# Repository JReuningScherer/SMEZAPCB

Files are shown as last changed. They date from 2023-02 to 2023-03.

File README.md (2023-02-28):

# Team Solar - SMEZA PCB Repository

This is the repository for the PCB for the SMEZA. 

Code for the SMEZA should not be stored here - put those files in the [Team-Solar](https://github.com/kyperrone/Team-Solar) repo. 

We are using KiCad 7 for this project, as well as the following extensions:
- Freerouting extension, provided by the Official KiCad Repository. 
- Bounti's JLCPCB extension. This is in a [separate repository](https://github.com/Bouni/kicad-jlcpcb-tools) that must be added. 

# Explaination of Contents 
`smeza_pcb` - This folder contains the KiCad project files for the SMEZA PCB. 

`footprints` - This folder contains all of the project specific footprints in a convenient location. The footprint names in this folder are less than useful, so there is a README file that indicates which file is for which component. 

`symbols` - This folder contains all of the project specific symbols and footprints. Each component has its own folder. 

# Getting Started with using this repo 
I don't know how familiar everyone is with Git so I'm going to say a few things that are probably obvious to more experienced users. 

The primary branch for this repo is `main`. 

Please don't commit directly to main; make a branch for your changes and then when you are done make a pull-request. 

When possible, it is preferred that you obtain this repo by cloning it. However, since most Valpo machines do not have git it may be necessary to download the files and then try to merge after the fact. This is another good time to use a branch incase things get messed up. It should be noted that the 4-machines in the team solar senior design space have git installed - just make sure to use the git-bash terminal. 

While the KiCad files are technically text files, because of the large scale of changes made by even small changes, best practice is probably to clobber everything in `main` with the contents of the newer branch. 

If you have questions about using git, talk to Joel.

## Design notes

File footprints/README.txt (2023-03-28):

Tranceiver: ADM4852ARZ.kicad_mod

H-Bridge: SOIC100P600X175-10N.kicad_mod
H-Bridge Alternate: A3909GLYTR-T.kicad_mod

Buck Converter (MP4541): SOIC127P600X170-9N.kicad_mod

RJ-45: SS90000002.kicad_mod

Oscillator: OSC_CSTNE16M0V530000R0.kicad_mod

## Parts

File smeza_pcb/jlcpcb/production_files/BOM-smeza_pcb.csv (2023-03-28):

Comment | Designator | Footprint | LCSC
10uF | C2A1,C2B1,C8 | C_1206_3216Metric | C13585
ATmega328P-A | U2 | TQFP-32_7x7mm_P0.8mm | C14877
100k | R8 | R_0805_2012Metric | C149504
680pF | C1 | C_0603_1608Metric | C1630
1.2k | R1 | R_0805_2012Metric | C17379
1.8k | R6 | R_0805_2012Metric | C17398
10k | R14,R15,R2 | R_0805_2012Metric | C17414
120 | R22,R4 | R_0805_2012Metric | C17437
2.2k | R16,R17 | R_0805_2012Metric | C17520
27k | R12,R13 | R_0805_2012Metric | C17593
4.7k | R19,R20,R21 | R_0805_2012Metric | C17673
82k | R10,R11,R7 | R_0805_2012Metric | C17840
1uF | C5,C6 | C_1206_3216Metric | C1848
33uH | L1 | L_Taiyo-Yuden_NR-60xx_HandSoldering | C2049900
LED | D1 | LED_0603_1608Metric | C2286
0.1uF | C3,C4,C7 | C_1206_3216Metric | C24497
39k | R18 | R_0805_2012Metric | C25826
H_Bridge | H1 | SOIC100P600X175-10N | C2653462
CSTNE16M0V530000R0 | Y1 | OSC_CSTNE16M0V530000R0 | C341521
5.6k | R5,R9 | R_0805_2012Metric | C4382
1k | R3 | R_1206_3216Metric | C4410
2.2uF | C2 | C_1206_3216Metric | C50254
1nF | C10,C11,C9 | C_1206_3216Metric | C9196
MP4541GN-Z | B1 | SOIC127P600X170-9N
LM317_TO-220 | U1 | TO-220-3_Vertical

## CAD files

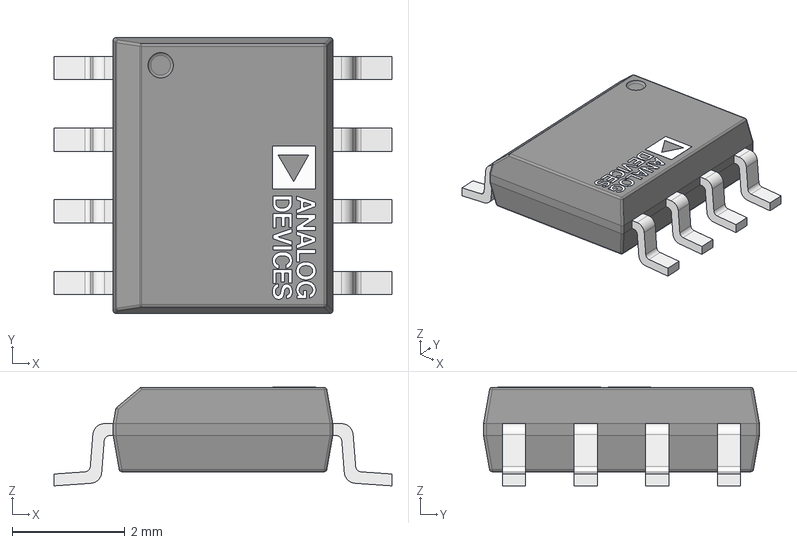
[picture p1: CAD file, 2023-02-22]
symbols/ADM4852ARZ/eec.models/Analog_Devices_-_ADM4852ARZ.step
6.00 x 4.90 x 1.75 mm
pins
part number

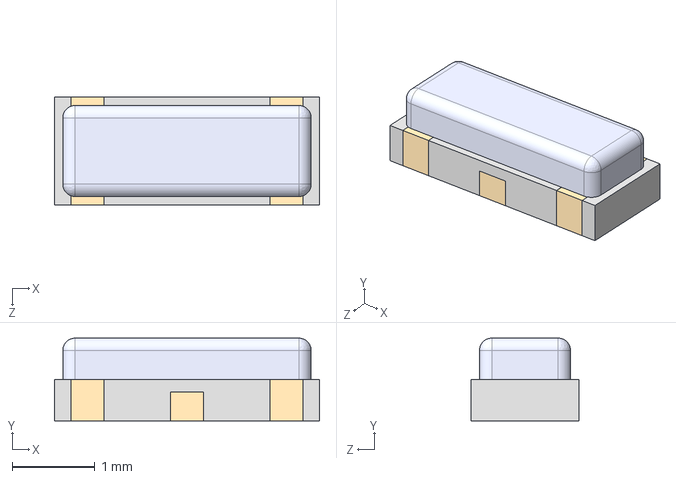
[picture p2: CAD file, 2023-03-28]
symbols/CSTNE16M0V530000R0/CSTNE16M0V530000R0.step
3.20 x 1.00 x 1.30 mm

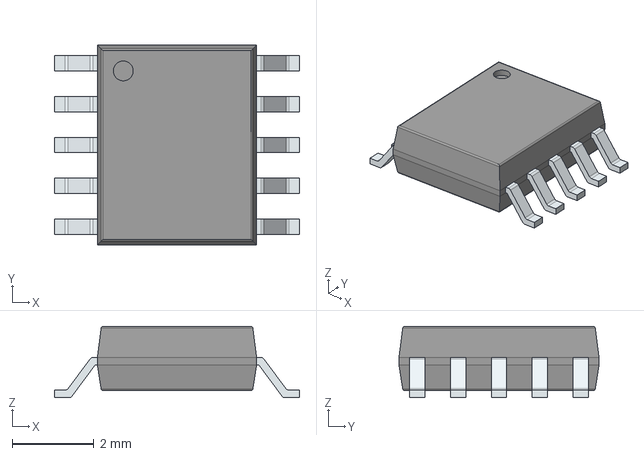
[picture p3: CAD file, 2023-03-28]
symbols/LIB_A3909GLNTR-T/A3909GLNTR-T/3D/A3909GLNTR-T.stp
6.00 x 4.90 x 1.75 mm
PinsArrayLR

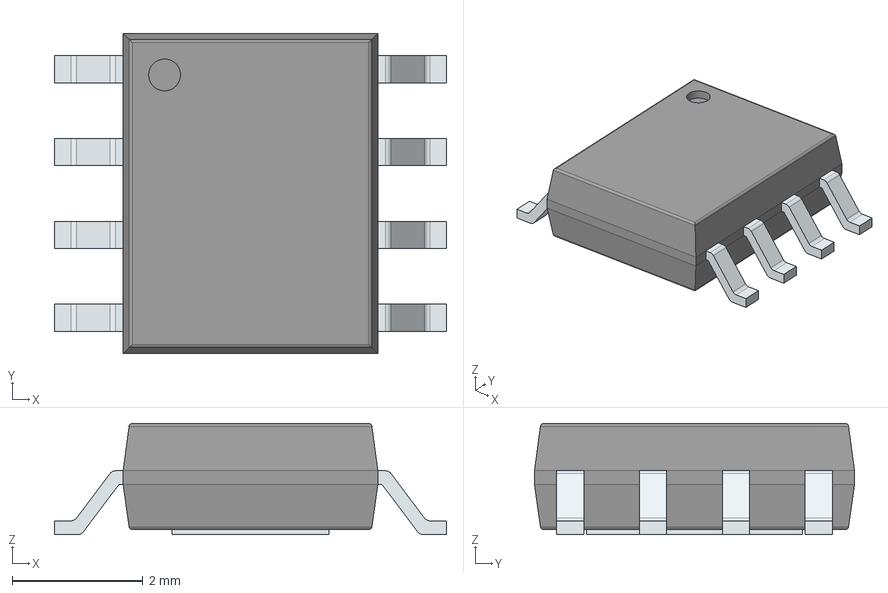
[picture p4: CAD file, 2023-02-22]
symbols/LIB_MP4541GN-Z/MP4541GN-Z/3D/MP4541GN-Z.stp
6.00 x 4.90 x 1.70 mm
PinsArrayLR
ThermalPad

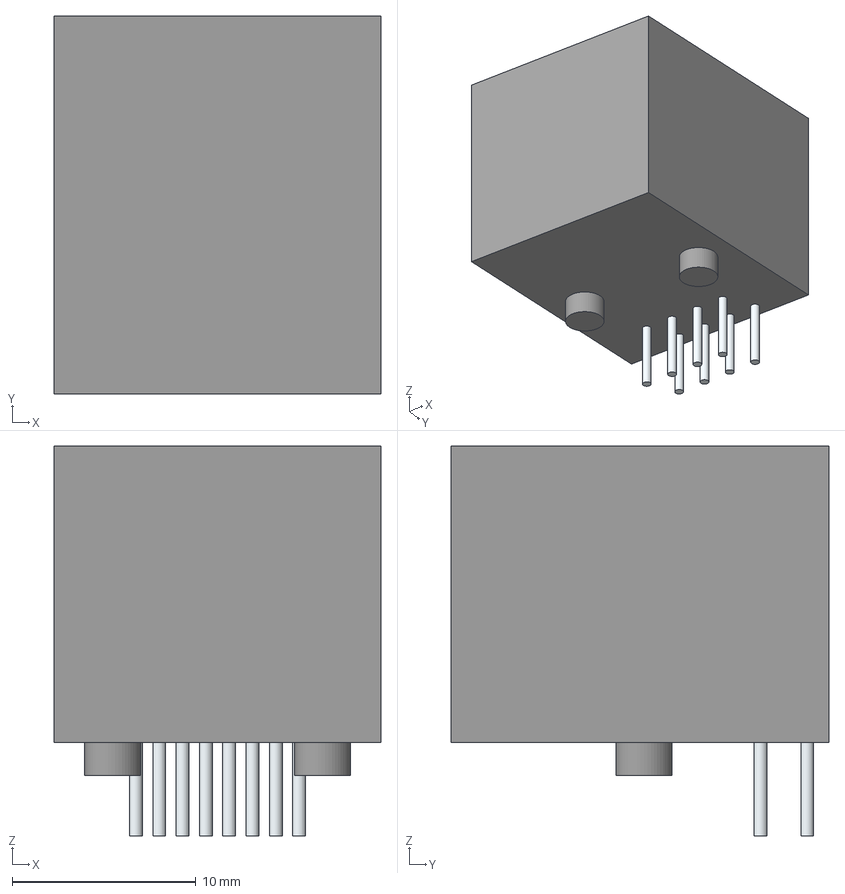
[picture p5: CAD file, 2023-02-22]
symbols/LIB_SS-90000-002/SS-90000-002/3D/SS-90000-002.stp
17.8 x 20.6 x 21.2 mm
Lugs
Leads

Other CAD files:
symbols/LIB_A3909GLNTR-T/A3909GLNTR-T/Allegro/sop100p600x175-10n.psm
symbols/LIB_A3909GLNTR-T/A3909GLNTR-T/DEHDL/a3909glntr_t/chips/chips.prt
symbols/LIB_MP4541GN-Z/MP4541GN-Z/Allegro/soic127p600x170-9n.psm
symbols/LIB_MP4541GN-Z/MP4541GN-Z/DEHDL/mp4541gn_z/chips/chips.prt
symbols/LIB_SS-90000-002/SS-90000-002/Allegro/ss90000002.psm
symbols/LIB_SS-90000-002/SS-90000-002/DEHDL/ss_90000_002/chips/chips.prt

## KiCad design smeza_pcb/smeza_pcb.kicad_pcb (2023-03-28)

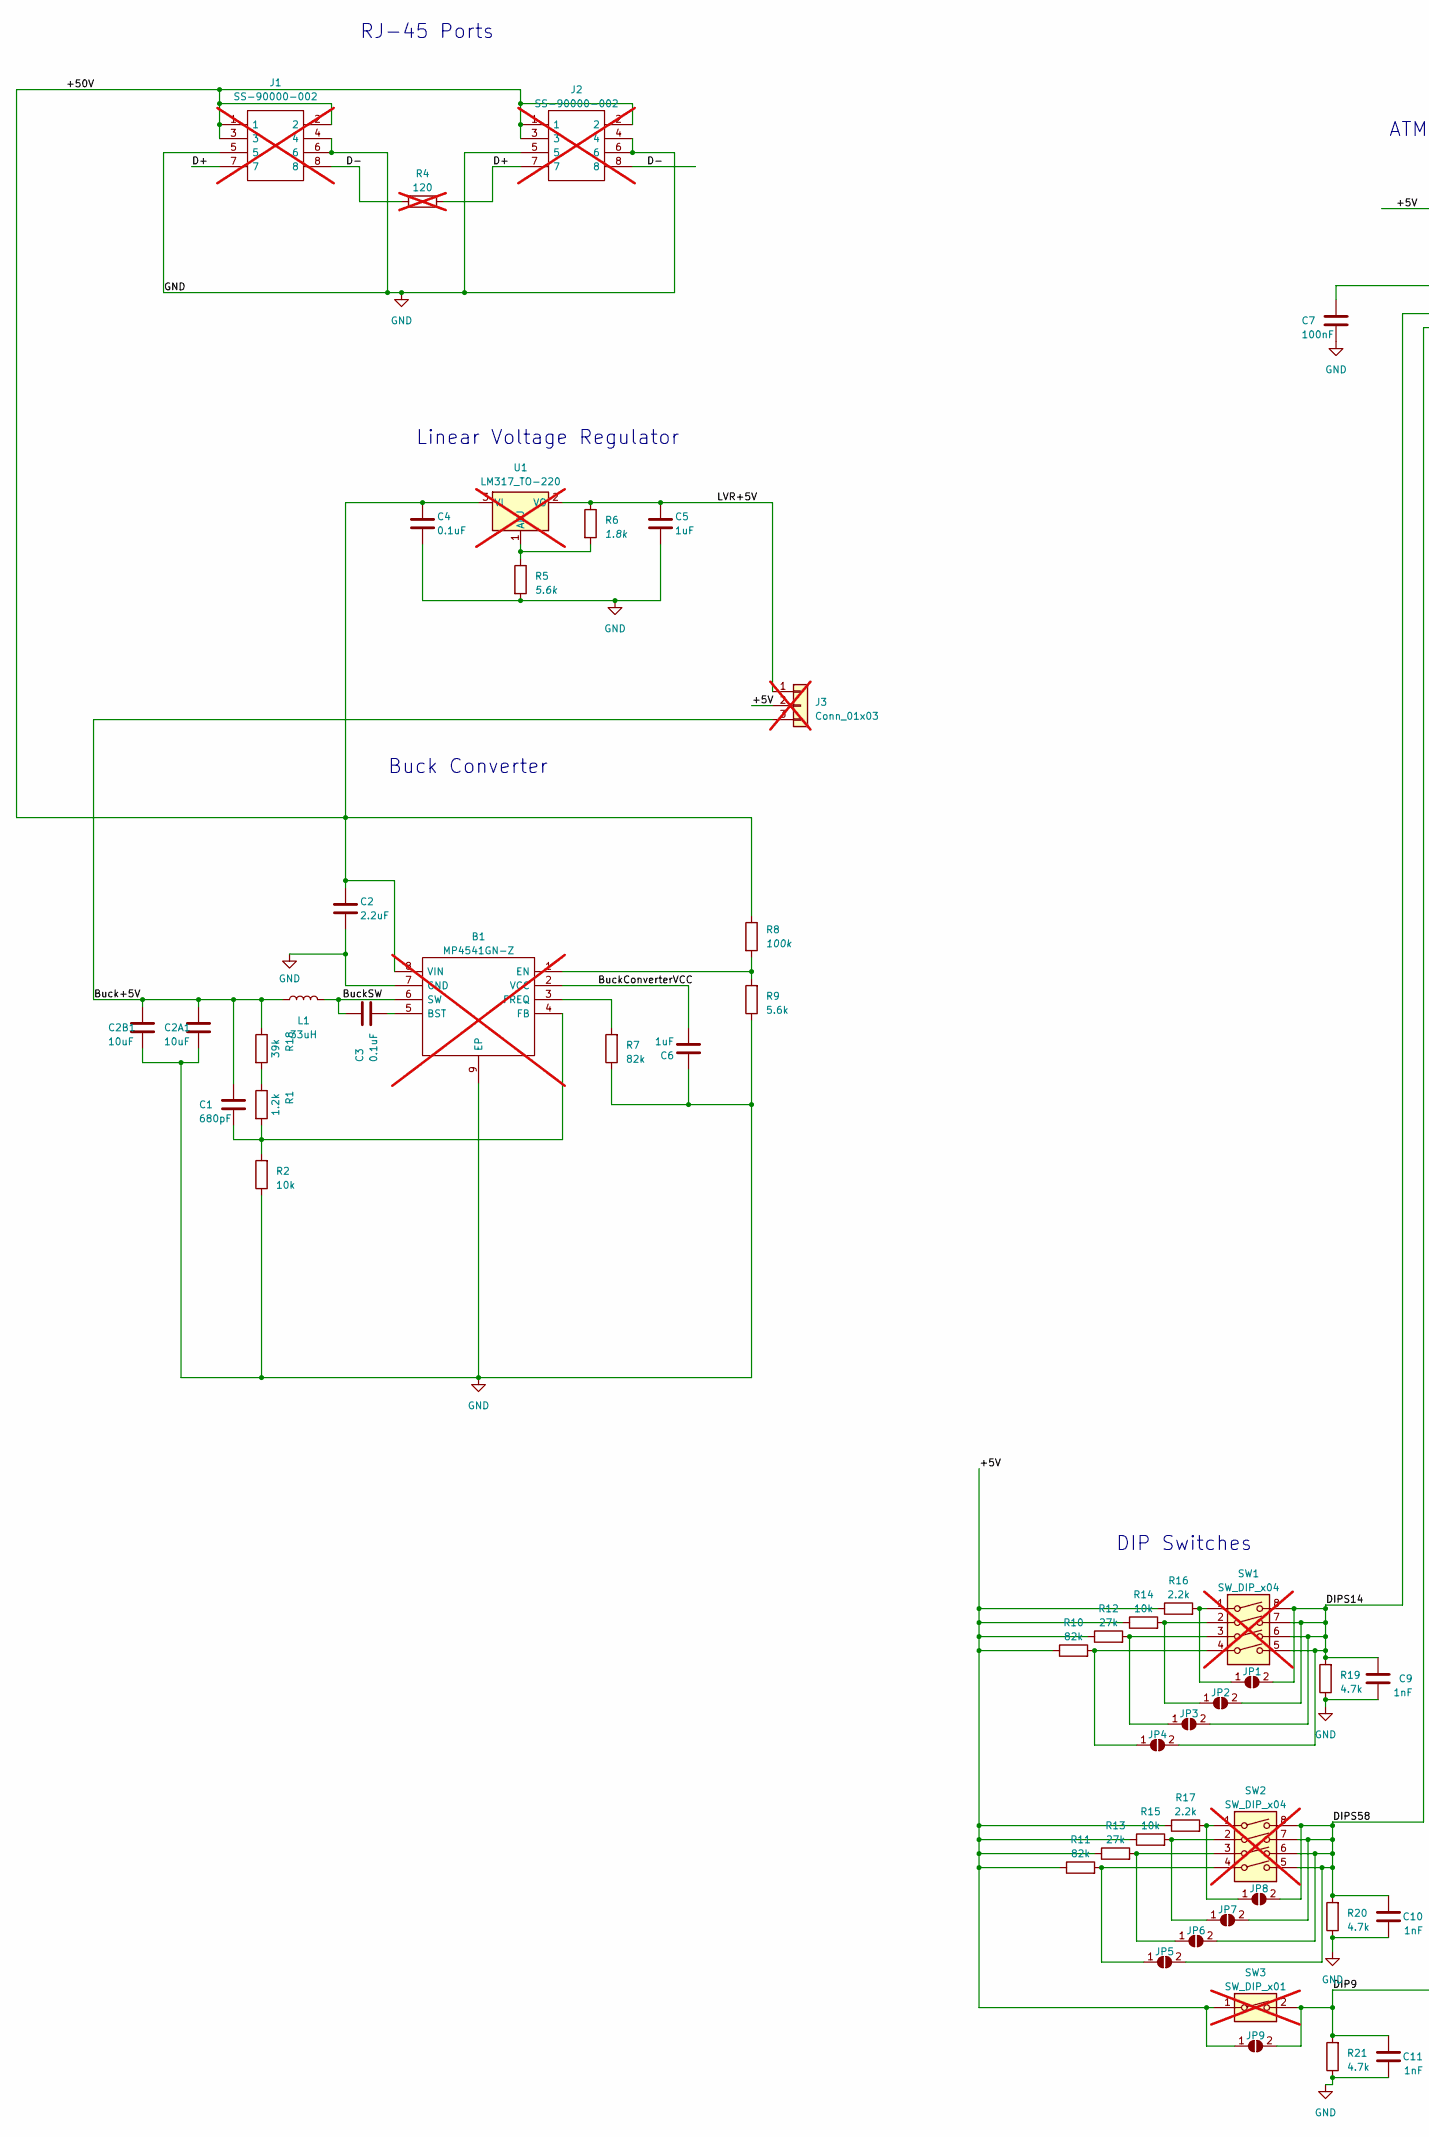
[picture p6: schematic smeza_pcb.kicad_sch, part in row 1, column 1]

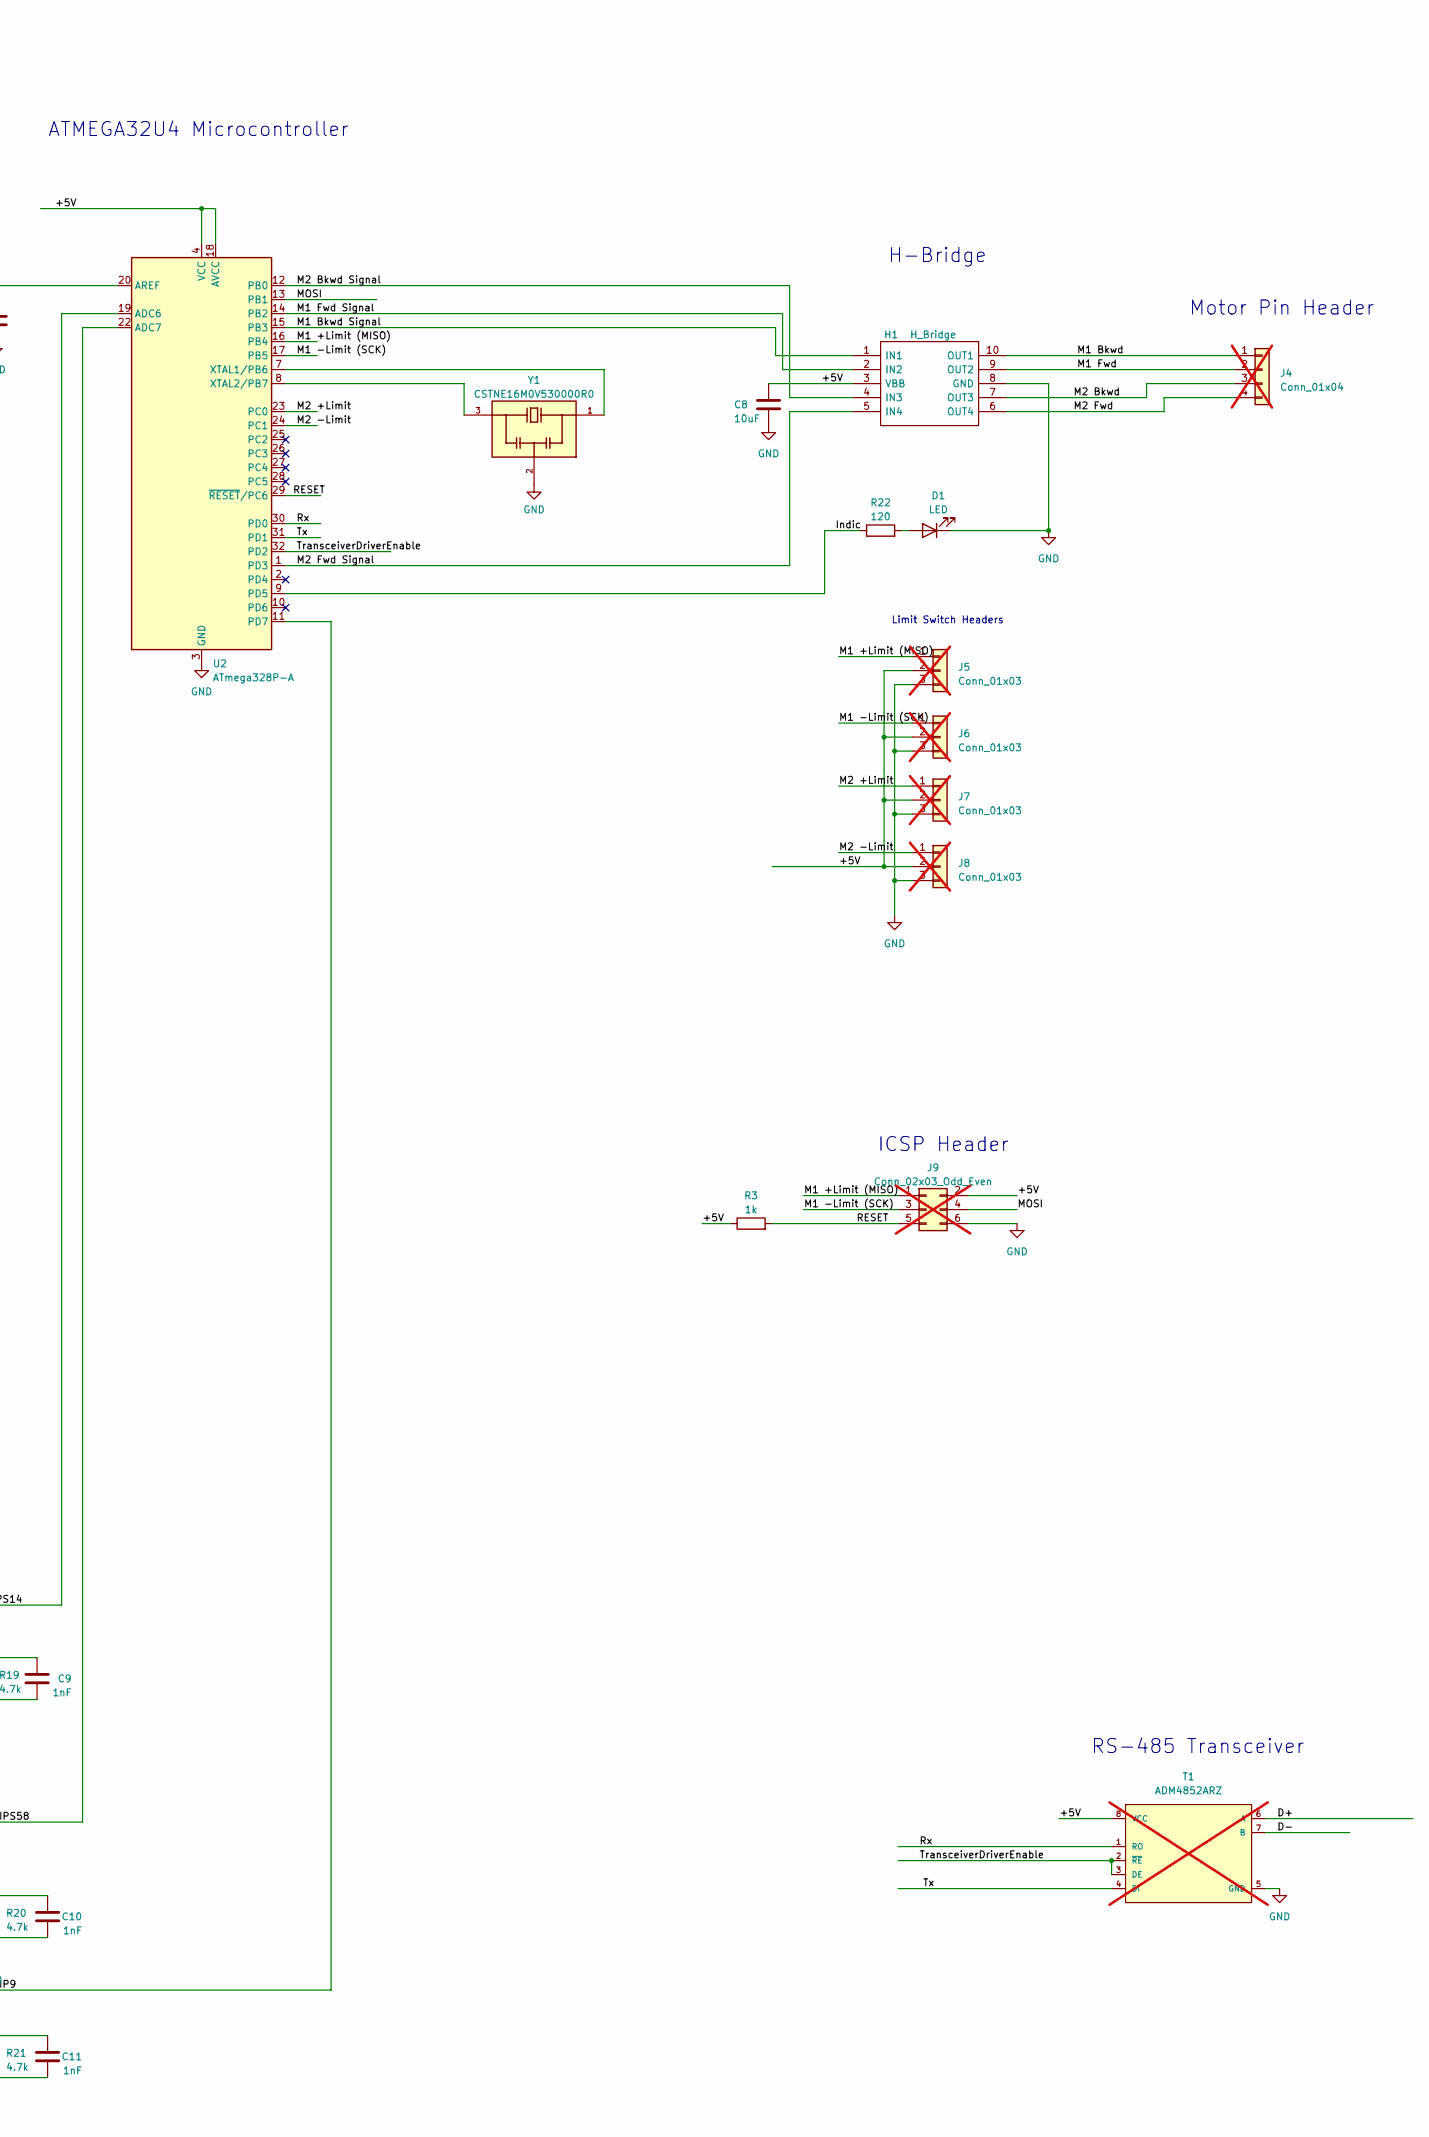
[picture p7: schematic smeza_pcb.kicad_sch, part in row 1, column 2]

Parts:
B1: MP4541GN-Z; SOIC127P600X170-9N; Mouser Part Number 946-MP4541GN-Z; not fitted
C1: 680pF; C_0603_1608Metric
C2: 2.2uF; C_1206_3216Metric
C2A1, C2B1, C8: 10uF; C_1206_3216Metric
C3, C4: 0.1uF; C_1206_3216Metric
C5, C6: 1uF; C_1206_3216Metric
C7: 100nF; C_1206_3216Metric
C9, C10, C11: 1nF; C_1206_3216Metric
D1: LED; LED_0603_1608Metric
H1: H_Bridge; SOIC100P600X175-10N; Manufacturer_Part_Number A3909GLNTR-T; Mouser Part Number 250-A3909GLNTR-T
J1, J2: SS-90000-002; SS90000002; Mouser Part Number 530-SS-90000-002; not fitted
J3: Conn_01x03; PinHeader_1x03_P2.54mm_Vertical; not fitted
J4: Conn_01x04; Molex_KK-254_AE-6410-04A_1x04_P2.54mm_Vertical; not fitted
J5, J6, J7, J8: Conn_01x03; Molex_KK-254_AE-6410-03A_1x03_P2.54mm_Vertical; not fitted
J9: Conn_02x03_Odd_Even; PinHeader_2x03_P2.54mm_Vertical; not fitted
JP1, JP2, JP3, JP4, JP5, JP6, JP7, JP8, JP9: SolderJumper_2_Open; SolderJumper-2_P1.3mm_Open_TrianglePad1.0x1.5mm
L1: 33uH; L_Taiyo-Yuden_NR-60xx_HandSoldering
R1: 1.2k; R_0805_2012Metric
R2, R14, R15: 10k; R_0805_2012Metric
R3: 1k; R_1206_3216Metric
R4: 120; R_0805_2012Metric; not fitted
R5, R9: 5.6k; R_0805_2012Metric
R6: 1.8k; R_0805_2012Metric
R7, R10, R11: 82k; R_0805_2012Metric
R8: 100k; R_0805_2012Metric
R12, R13: 27k; R_0805_2012Metric
R16, R17: 2.2k; R_0805_2012Metric
R18: 39k; R_0805_2012Metric
R19, R20, R21: 4.7k; R_0805_2012Metric
R22: 120; R_0805_2012Metric
SW1, SW2: SW_DIP_x04; SW_DIP_SPSTx04_Slide_9.78x12.34mm_W7.62mm_P2.54mm; not fitted
SW3: SW_DIP_x01; SW_DIP_SPSTx01_Slide_9.78x4.72mm_W7.62mm_P2.54mm; not fitted
T1: ADM4852ARZ; mouser part number 584-ADM4852ARZ; digikey description IC TRANSCEIVER HALF 1/1 8SOIC; not fitted
U1: LM317_TO-220; TO-220-3_Vertical; not fitted
U2: ATmega328P-A; TQFP-32_7x7mm_P0.8mm
Y1: CSTNE16M0V530000R0; OSC_CSTNE16M0V530000R0; PARTREV JGC42-8853B

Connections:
/+5V: C8.1, H1.3 (VBB), J3.2, J5.2, J6.2, J7.2, J8.2, J9.2, JP9.1 (A), R3.1, R10.1, R11.1, R12.1, R13.1, R14.1, R15.1, R16.1, R17.1, SW3.1, T1.8 (VCC), U2.4 (VCC), U2.6 (VCC), U2.18 (AVCC)
/+50V: B1.8 (VIN), C2.1, C4.1, J1.1, J1.2, J1.3, J2.1, J2.2, J2.3, R8.1, U1.3 (VI)
/Buck+5V: C1.1, C2A1.1, C2B1.1, J3.3, L1.1, R18.1
/BuckConverterVCC: B1.2 (VCC), C6.2
/BuckSW: B1.6 (SW), C3.1, L1.2
/D+: J1.7, J2.7, R4.1, T1.6 (A)
/D-: J1.8, J2.8, R4.2, T1.7 (B)
/DIP9: C11.1, JP9.2 (B), R21.2, SW3.2, U2.11 (PD7)
/DIPS14: C9.1, JP1.2 (B), JP2.2 (B), JP3.2 (B), JP4.2 (B), R19.2, SW1.5, SW1.6, SW1.7, SW1.8, U2.19 (ADC6)
/DIPS58: C10.1, JP5.2 (B), JP6.2 (B), JP7.2 (B), JP8.2 (B), R20.2, SW2.5, SW2.6, SW2.7, SW2.8, U2.22 (ADC7)
/Indic: R22.1, U2.9 (PD5)
/LVR+5V: C5.1, J3.1, R6.1, U1.2 (VO)
/M1 +Limit (MISO): J5.1, J9.1, U2.16 (PB4)
/M1 -Limit (SCK): J6.1, J9.3, U2.17 (PB5)
/M1 Bkwd: H1.10 (OUT1), J4.1
/M1 Bkwd Signal: H1.1 (IN1), U2.15 (PB3)
/M1 Fwd: H1.9 (OUT2), J4.2
/M1 Fwd Signal: H1.2 (IN2), U2.14 (PB2)
/M2 +Limit: J7.1, U2.23 (PC0)
/M2 -Limit: J8.1, U2.24 (PC1)
/M2 Bkwd: H1.7 (OUT3), J4.3
/M2 Bkwd Signal: H1.4 (IN3), U2.12 (PB0)
/M2 Fwd: H1.6 (OUT4), J4.4
/M2 Fwd Signal: H1.5 (IN4), U2.1 (PD3)
/MOSI: J9.4, U2.13 (PB1)
/RESET: J9.5, R3.2, U2.29 (~RESET/PC6)
/Rx: T1.1 (RO), U2.30 (PD0)
/TransceiverDriverEnable: T1.2 (~RE), T1.3 (DE), U2.32 (PD2)
/Tx: T1.4 (DI), U2.31 (PD1)
GND: B1.7 (GND), B1.9 (EP), C2.2, C2A1.2, C2B1.2, C4.2, C5.2, C6.1, C7.2, C8.2, C9.2, C10.2, C11.2, D1.1 (K), H1.8 (GND), J1.4, J1.5, J1.6, J2.4, J2.5, J2.6, J5.3, J6.3, J7.3, J8.3, J9.6, R2.1, R5.2, R7.1, R9.1, R19.1, R20.1, R21.1, T1.5 (GND), U2.3 (GND), U2.5 (GND), U2.21 (GND), Y1.2
unnamed: B1.5 (BST), C3.2
unnamed: B1.1 (EN), R8.2, R9.2
unnamed: B1.4 (FB), C1.2, R1.2, R2.2
unnamed: B1.3 (FREQ), R7.2
unnamed: D1.2 (A), R22.2
unnamed: JP1.1 (A), R16.2, SW1.1
unnamed: JP2.1 (A), R14.2, SW1.2
unnamed: JP3.1 (A), R12.2, SW1.3
unnamed: JP4.1 (A), R10.2, SW1.4
unnamed: JP5.1 (A), R11.2, SW2.4
unnamed: JP6.1 (A), R13.2, SW2.3
unnamed: JP7.1 (A), R15.2, SW2.2
unnamed: JP8.1 (A), R17.2, SW2.1
unnamed: R1.1, R18.2
unnamed: R5.1, R6.2, U1.1 (ADJ)
unnamed: C7.1, U2.20 (AREF)
unnamed: U2.7 (XTAL1/PB6), Y1.1
unnamed: U2.8 (XTAL2/PB7), Y1.3

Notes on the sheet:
H-Bridge
DIP Switches
Buck Converter
ATMEGA32U4 Microcontroller
ICSP Header
Motor Pin Header
RS-485 Transceiver
RJ-45 Ports
Limit Switch Headers
Linear Voltage Regulator

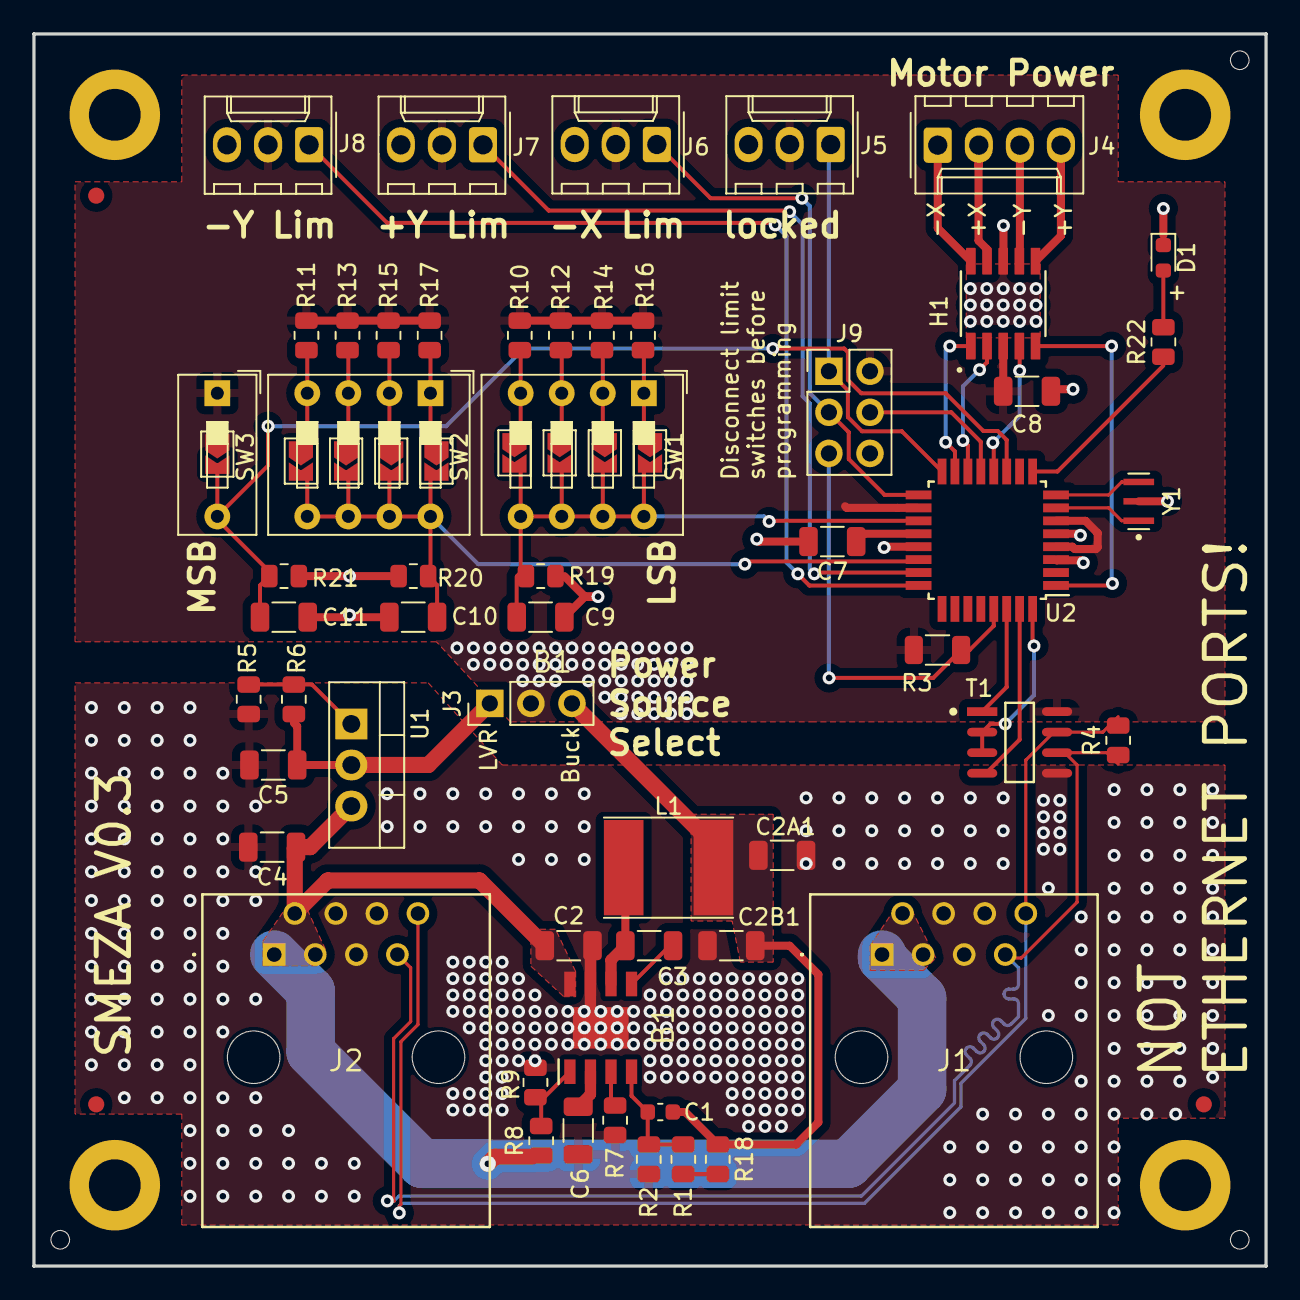
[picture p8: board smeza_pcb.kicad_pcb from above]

Board: 2 copper layers, 76.2 x 76.2 mm, 67 parts (0 on the bottom side), 48 nets.

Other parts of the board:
FAB**: ToolingHole
FAB**#2, FAB**#3: ToolingHole

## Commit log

2023-02-22 Initial Commit. Added KiCad Files, Footprints, Symbols.
    [BOM-smeza_pcb_v3.csv, freerouting.dsn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]
2023-02-22 Actually added KiCad, Footprints, Symbols. Forgot to stage changes.
    [Analog_Devices_-_ADM4852ARZ.step, EDI2CAP.CFG, MP4541GN-Z.SchLib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]
2023-02-23 Changed library paths from absolute paths to relative paths. Attempted to fix issue referencing old versions of the schematic.
    [smeza_pcb.kicad_sch]
2023-02-24 Corrected Footprints in Schematic. Reorganized passives supporting the buck converter. Rerouted 50V passthough, D+/- passthrough.
    [smeza_pcb.kicad_pcb, smeza_pcb.kicad_sch]
2023-03-07 Reorganized all components and rerouted. Added capacitors to H-Bridge. Added Capacitors to dip switches. Updated DIP switch footprint. Fixed DRC and ERC errors.
    [smeza_pcb.kicad_pcb, smeza_pcb.kicad_sch]
2023-03-07 Resized traces for SW2.
    [smeza_pcb.kicad_pcb]
2023-03-07 Finalized LCSC Part Numbers
    [smeza_pcb-CuBottom.gbr, smeza_pcb-CuTop.gbr, smeza_pcb-EdgeCuts.gbr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]
2023-03-07 Footprint and Symbol Updates
    [A3909GLNTR-T.SchLib, A3909GLNTR-T.stp, CSTNE16M0V530000R0.step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]
2023-03-07 Included Output Files
    [BOM-smeza_pcb.csv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]
2023-03-11 Moved vias out from under pads
    [smeza_pcb.kicad_pcb]
2023-03-11 Updated version text on board
    [smeza_pcb.kicad_pcb]
2023-03-11 Separated MOSI and M2 Bkwd pins
    [smeza_pcb.kicad_pcb, smeza_pcb.kicad_sch]
2023-03-11 Replaced most extended parts. Swapped out many 1206 resistors for 0805 resistors. Swapped out C1. Swapped out LED. Made all headers DNP. Rerouted to reflect the new footprints.
    [BOM-smeza_pcb.csv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]
2023-03-11 Added tooling holes
    [smeza_pcb.kicad_pcb]
2023-03-11 Added fiducials and checked component spacing. Removed old JLCPCB files
    [BOM-smeza_pcb_v3.csv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]
2023-03-11 Fixed part rotations. Fixed silkscreen goofs. Added solder jumpers.
    [BOM-smeza_pcb.csv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]
